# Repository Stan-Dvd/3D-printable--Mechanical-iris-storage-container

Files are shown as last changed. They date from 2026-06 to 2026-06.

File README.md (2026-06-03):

# Mechanical Iris Storage Container
Storage container with dual-plane iris closing mechanism
## Showcase
### Renders:
<p align="center">
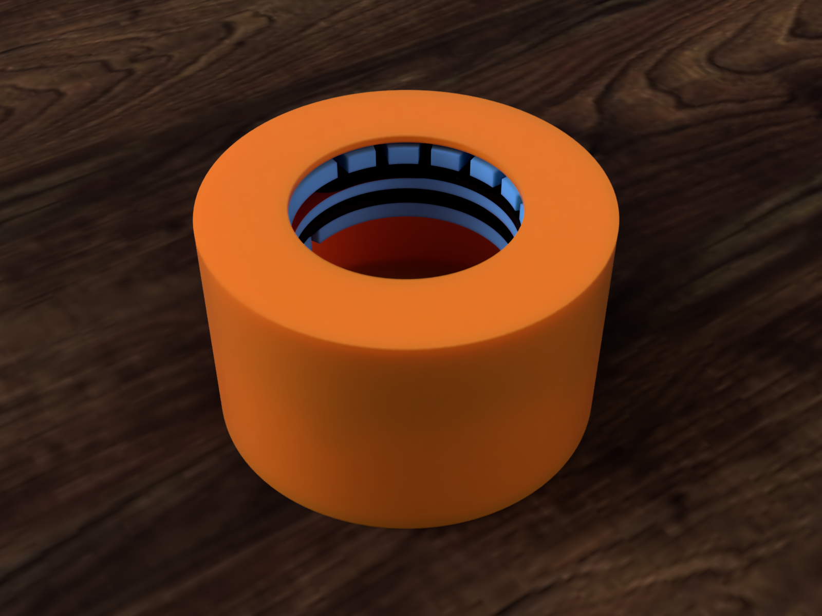
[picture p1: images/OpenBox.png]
  
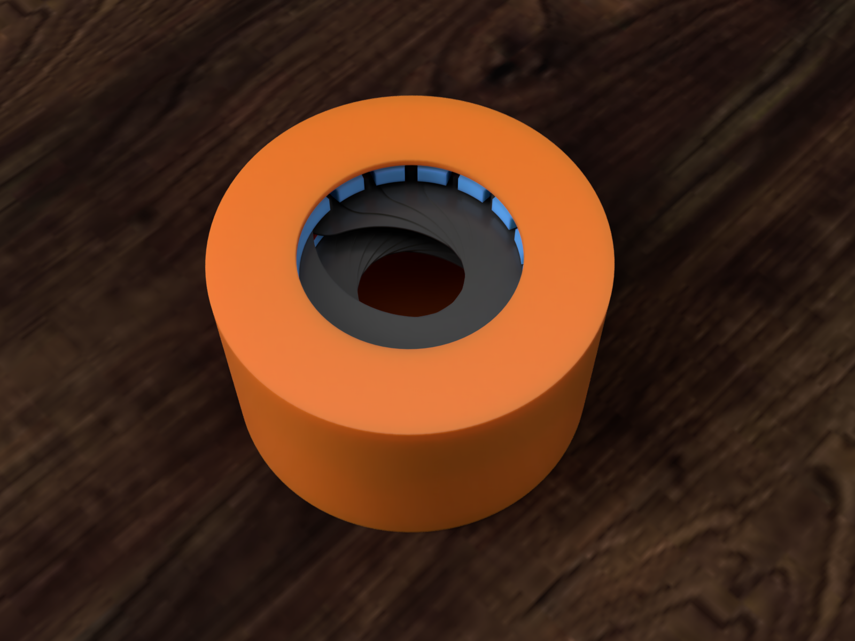
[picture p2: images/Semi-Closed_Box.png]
  
</p>

### Demo video:
Container Demo (https://youtu.be/vQDJuscBDms)

# In short
The basic idea of the project was to create a circular container with a rotating lid that opens and closes an iris mechanism of some form, upon rotating the lid. The idea started upon seeing [this](https://www.printables.com/model/514762-mechanical-iris-container) model on printables (pictured below), and the research started from there

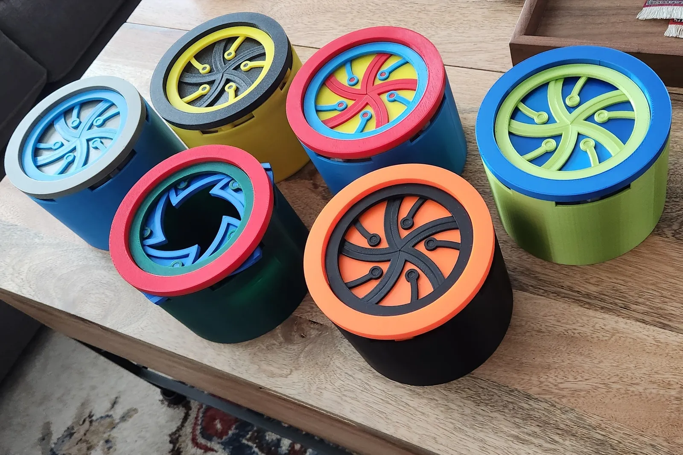
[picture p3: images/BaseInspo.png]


# Design process
The first step of the design process was deciding on the actual iris mechanism to use. The most important part about the mechanism was that I wanted it to be able to fully close. Starting from that, the one from the printables model above was interesting, but I disliked the fact that the blades fanned outward and I couldn't tell how I would build the trajectories for the blades to follow.  Throughout my research, I encountered many mechanisms similar to this one, which I came to name "Rotational translate" irises.
## "Sliding Iris"
The second type of mechanism I encountered was the "sliding iris", where the blades slide along a straight path to partially or completely cover the inner area of the iris. The design was practical and arguably the easiest to implement, but I disliked how once again, it either needed to have a very large ammount of space dedicated to storing the blades, or the blades would have to extend outside of the mechanism.

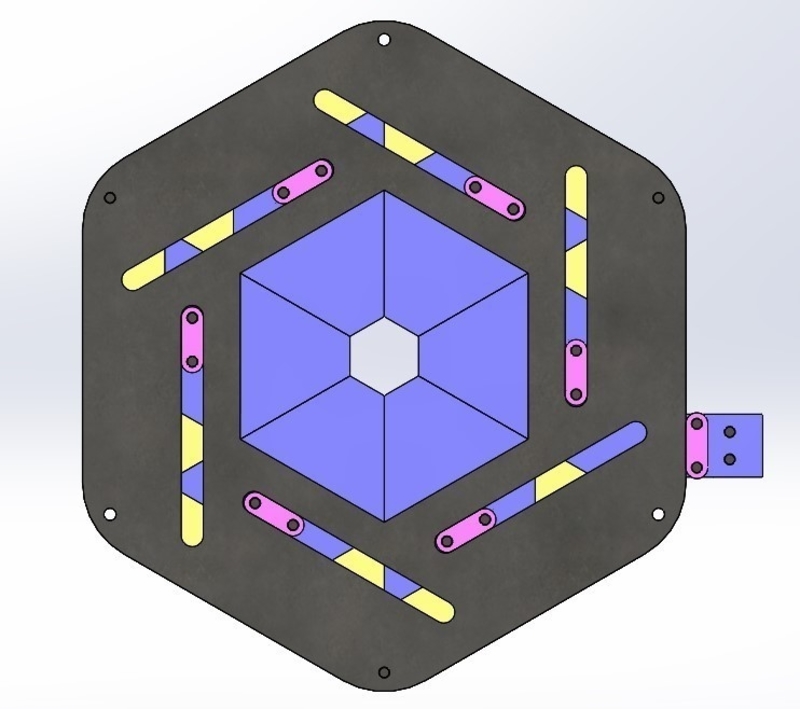
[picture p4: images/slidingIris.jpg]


## Apperture
The third option I found was the traditional camera apperture mechanism. It had the advantage of a small external area but these mechanisms are not designed to close completely. It could be smaller than the others and in theory the most advantageous but ultimately it failed to meet the first requirement - closing completely. This is when I found the mechanism I would eventually choose.

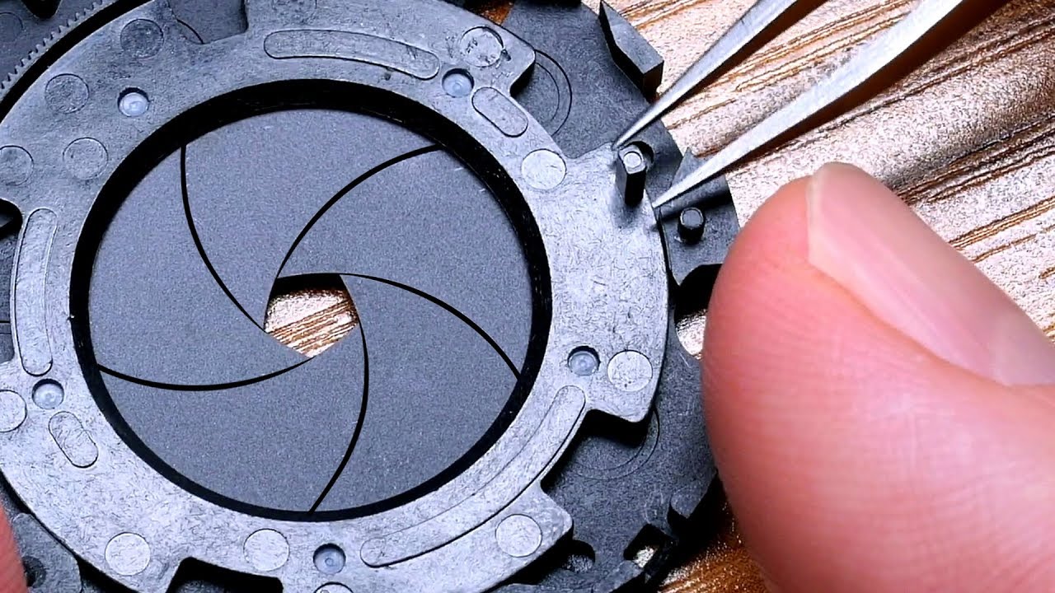
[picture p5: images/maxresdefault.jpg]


## Dual-Plane Iris
The mechanism I eventually chose was the Dual-Plane Iris. It functions very similarly to a regular apperture-type Iris and could generally be designed using the same principles, except it separated the blades into two planes. Half of the blades would sit on one plane, and the other half would sit on the other, while the actuator ring sat in the middle, driving them all. This prevented the blades from overlapping to the point where they wouldn't be able to close, and allowed for a fully closing mechanism

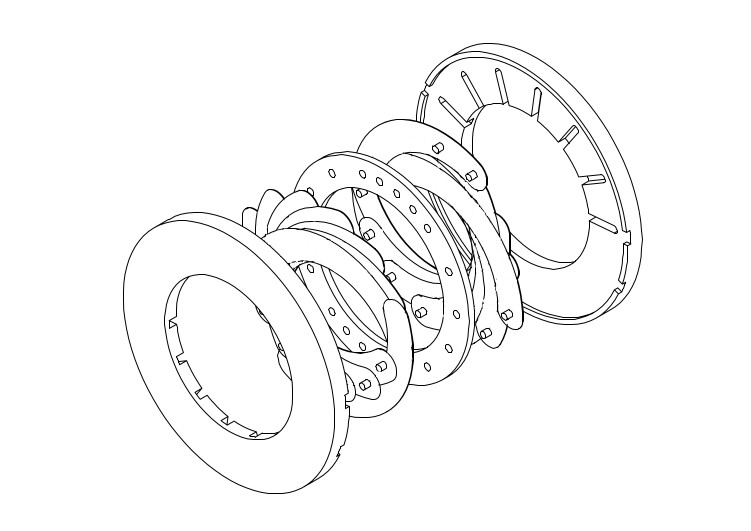
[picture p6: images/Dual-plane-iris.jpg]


# Parts
## Slide rings
The "slide rings" have two roles: allow the blades to move back and forth to follow the actuator ring, and define the axis around which they will be rotating. The dual-plane design requires two slide rings. On a normal apperture mechanism, all of the slots would be on one single ring, but this design places half of the slots on one ring, and half of the slots on the other. The slots on the sides are practically just for the top ring. The body will have two pins that will hold the top ring in place. On that note, it is essential that both slide rings are held in place, the actuator is the only ring that should rotate. However, the slots are found on all the other rings to allow them to be inserted into the body. Additionally, the bottom ring has pin holes on the bottom that will hold it in place relative to the body (not shown)

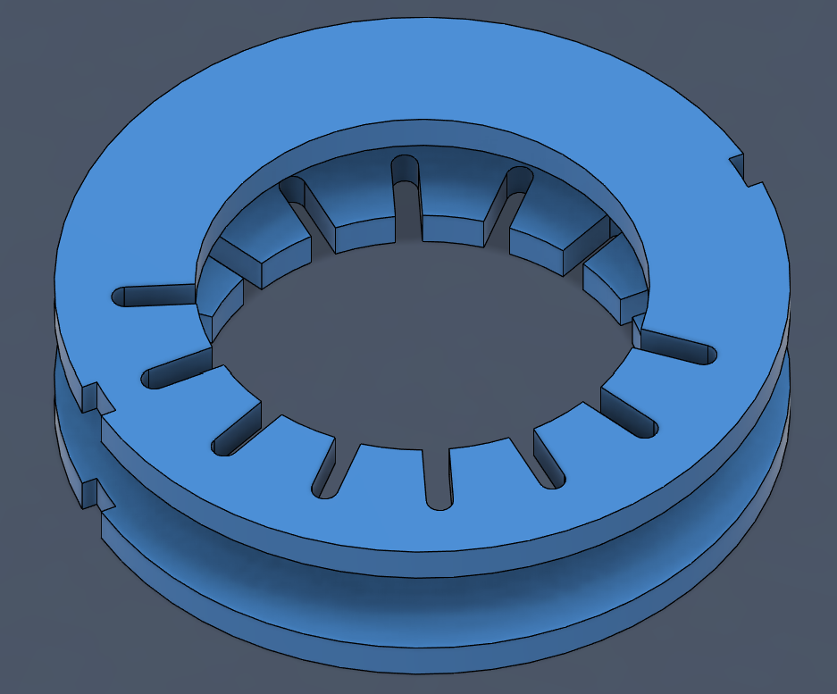
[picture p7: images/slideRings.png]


## Actuator ring
The actuator is the ring that moves the blades, "pulling" them along its' radius and making the iris close. On it, there are 16 pins for each of the regular blades, plus 4 pins that will hold two special "slip-blades", which will be explained later. The inner slots from the slide rings are prezent, as well as two additional outward slots. They will be used to spin the actuator ring from the lid of the container.
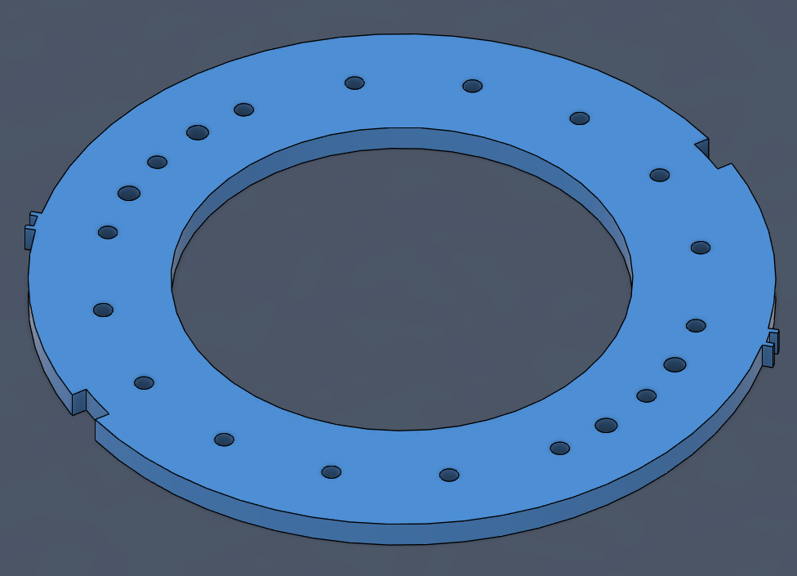
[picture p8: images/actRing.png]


## Blades
### Normal Blades

All of the blades have the same shape, but they differ in how their pins are placed. The bottom blades have their "slide pin" pointing downards and their "actuator pin" pointing upwards. The top blades have their orientations and positions reversed. Additionally, if we were to design the blades in one single piece, they would be very difficult to print because of the two pins on opposing sides. Printing with supports would greatly complicate things, as these pins should be as thin and clean as possible. As such, the actuator pin is to be printed separately, and glued on. To facilitate this, the blade itself has a hole and slot for the pin to fit into, which can be seen on one of the blades pictured below. Another thing to note is that the pins need to be quite long. The blades will be placed on top of each other, and so the pins need to be long enough to reach their respective rings from a decent distance, determined by the thickness and number of blades.

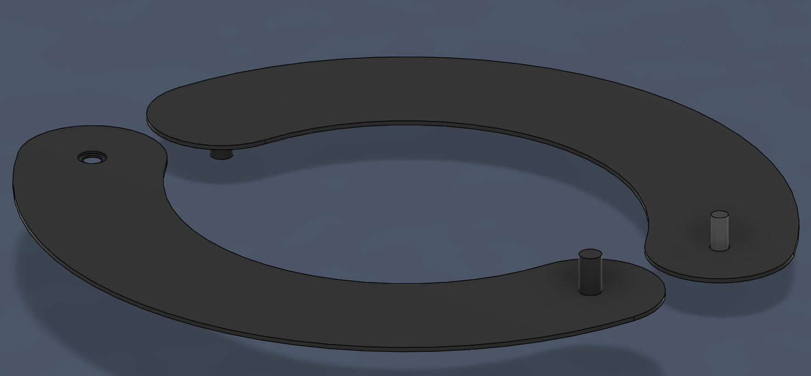
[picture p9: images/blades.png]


### Slip Blades
The slip blades have wo rigid pins on the same side of the blade, again mirroring the pins' position for the top and bottom. Their purpose is to sit on and along the actuator ring, to slip the blades above each other, so the actuator pins don't hit the slide pins. This will make more sense after the mechanism is presented

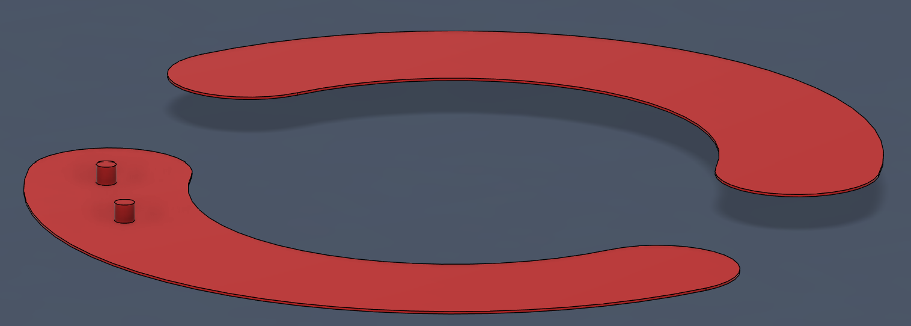
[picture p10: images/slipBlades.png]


## Container body
The container components are in many ways much simpler than the other parts. The container body is a simple cylinder with one side open and a few pins added for holding the top and bottom sliding rings. The bottom ring supports are chamfered at a 45 degree angle, to support 3D printing.

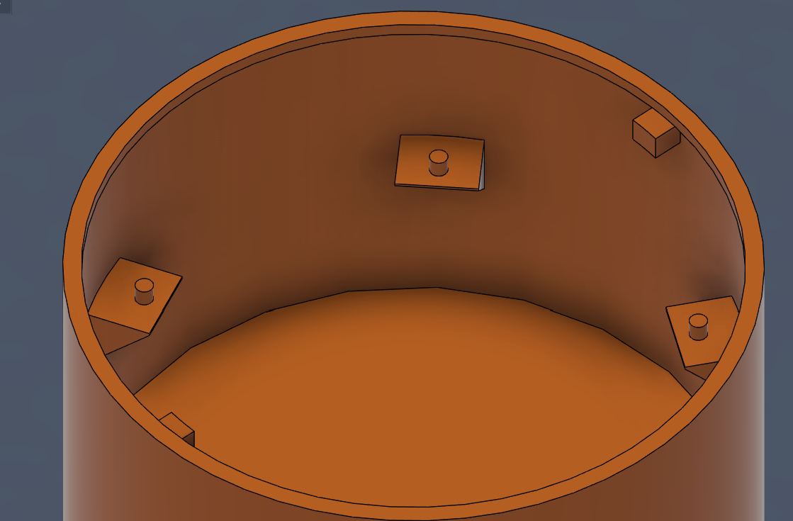
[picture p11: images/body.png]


## Container Cap
The container cap has its' outer diameter equal to the outer diameter of the container and its' inner diameter equal to the inner diameter of the iris mechanism. Additionally, it has an extrusion that is meant to make it slot into the container, without sliding off of it. On top of that, it has two extending pins that reach the actuator ring, so that when the container cap is spun, it spins the actuator ring along with it, practically opening and closing the container

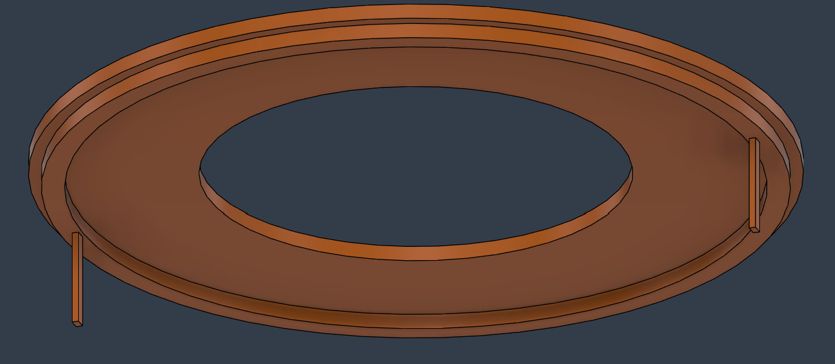
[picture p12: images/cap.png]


# Mechanism assembly and functioning
The blades are placed on top of each other, as shown, so that the slot pins don't hit any of the other blades. In reality, the blades would obviously not stay perfectly straight as shown, but would instead be dragged down by gravity and stay bent. That is intended. This is also the point in which the slip blades start to make sense. As the mechanism is right now, at about 65 degrees of rotation, the blade on the top would hit the slot pin of the blade on the bottom. 

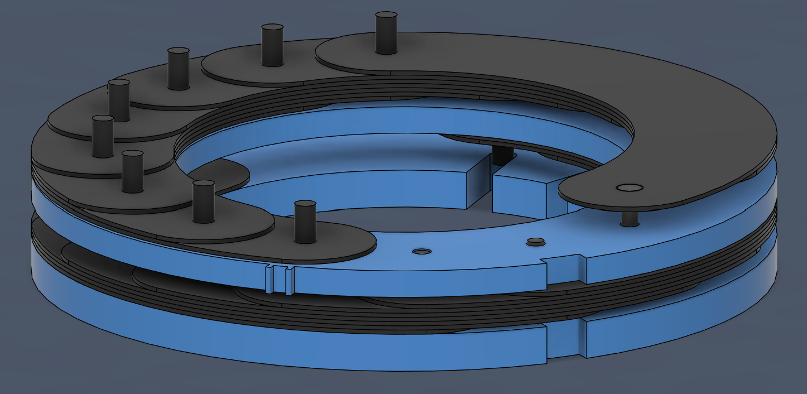
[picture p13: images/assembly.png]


To prevent this, the  slip blade is mounted directly on the actuator ring, below the first blade, and its' other end is placed above the top blade. As such, the top blade(s) will slide downard, below the bottom blade(s). Additionally, because the slip blade rotates with the actuator ring, the top blades do not run into the mounting pins of the slip blade. The slip blade is not shown, because it would have to be bent above the top blade, and I don't know if fusion can do that.
The functioning of the slip blade is similar for the bottom half.

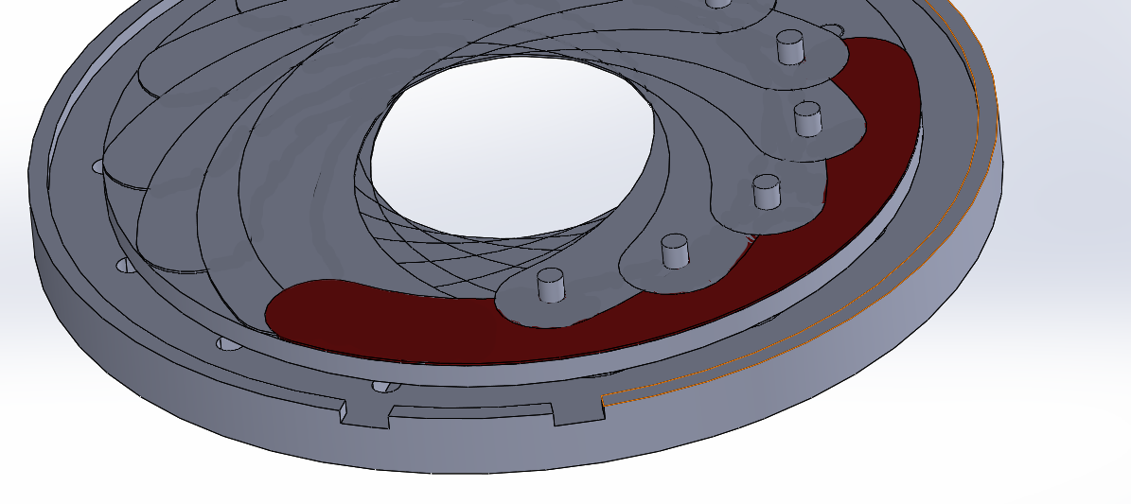
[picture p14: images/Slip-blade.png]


# Notes on the implementation and chosen dimensions
## Blade width 
As I have mentioned in the begining, I didn't want there to be too much space between the inner and outer diameter of the iris, and here, that depends on the width of the blades. Once again, the width of the blades depends on a few things. All of it starts with the closing diameter. The more you want the mechanism to close, logically, the more area the blades will need to cover. As such, the smaller the closing diameter, the thicker the blades need to be. However, this can be offset by the number of blades. A different way of covering the required area is to have more blades, allowing each individual blade to be thinner.
Originally, I started with a 12-blade design. However, once I had everything assembled and could test the entire mechanism, I noticed it didn't fully close. I experimented with making the blades wider, but ultimately felt I had to make them too thick. As such, I decided to switch over to a 16-blade design, and move to a new file. The blades are still wider than I'd like them to be, but I did not have time to experiment more before the deadline
## Blade height
In theory, the blades need to be as thin as possible. The height of the blades entirely determines the height of the entire mechanism, as the distance between each of the rings depends on the height of the blades and how many of them there are. On top of that, the blades cannot be too rigid, as they need to bend. Obviously, the more blades there are, the more critical it is for them to be as thin as possible

My problem in choosing the height of the blades was not knowing exactly how thin it would be reasonable to 3D print something, and how small details can be. Originally, I made the blades .4mm each, but I then realized I needed the slot and pin system to make the design printable. I was not sure if it would be reasonable to make the inner hole of the blade .2mm thick, so I made the blades .8mm and made the inner hole .4mm.
My problem with this is that because of the high thickness and the high number of blades, the iris mechanism itself is much, much taller than I would like it to be. However, I prefered to be safe, and left it like this for now
# Resources
https://www.printables.com/model/143497-mechanical-aperture/files
- base inspiration that sparked the idea for the entire project

https://www.youtube.com/watch?v=vCtbFtSfmnU&t=129s
- fusion tutorial for a 6-blade mechanical iris mechanism
- practically served as the foundation of the entire project

https://iris-calculator.com/full-closure/
 - main (and only) resource for dual-plane iris
 - includes [this](https://web.archive.org/web/20070207011241/http://www.wilkes-iris.com/flashIris/iris.htm) link to an interacteable demonstration of a dual-plane iris

https://www.youtube.com/watch?v=oH6GfyxpK9o 
- microscope aperture assembly, useful as a model for general assembly for these kinds of mechanisms

https://www.printables.com/model/143497-mechanical-aperture/files
- minor inspiration for 3D printed iris mechanism

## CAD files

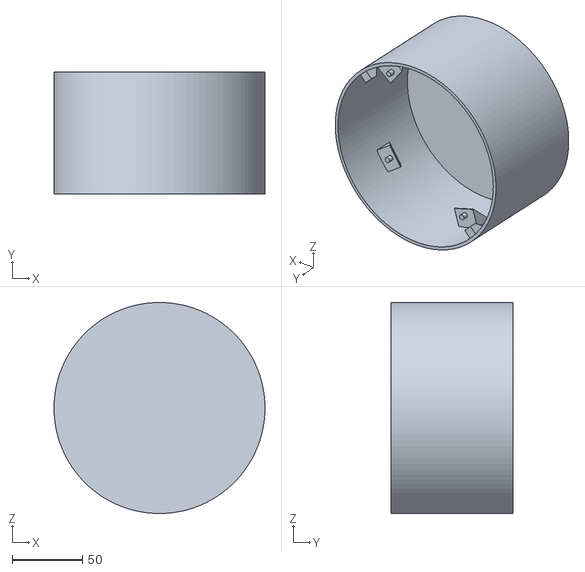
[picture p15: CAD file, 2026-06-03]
STL/Body.stl
150.0 x 87.0 x 150.0

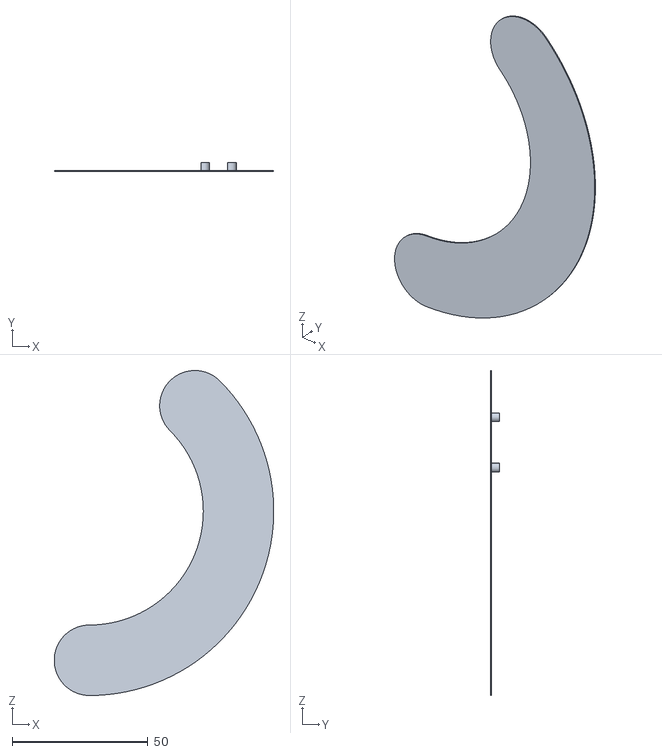
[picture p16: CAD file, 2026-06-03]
STL/SlipBladeBottom.stl
81.0 x 3.40 x 119.9

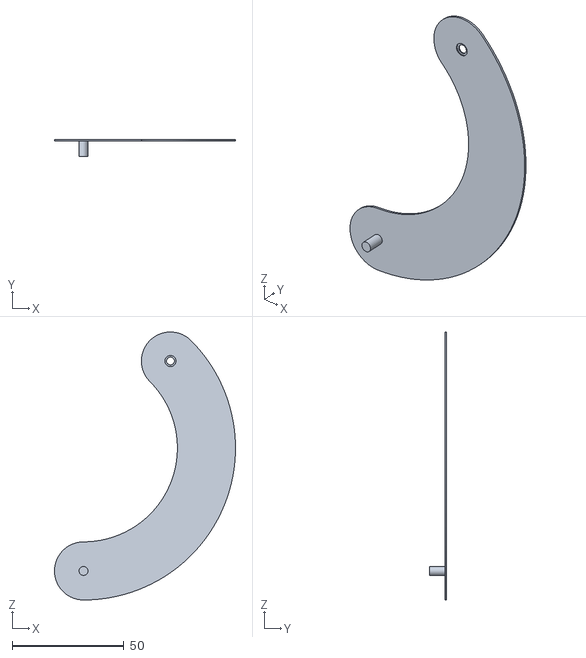
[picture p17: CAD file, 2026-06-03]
STL/BottomBlade.stl
81.0 x 7.80 x 119.9

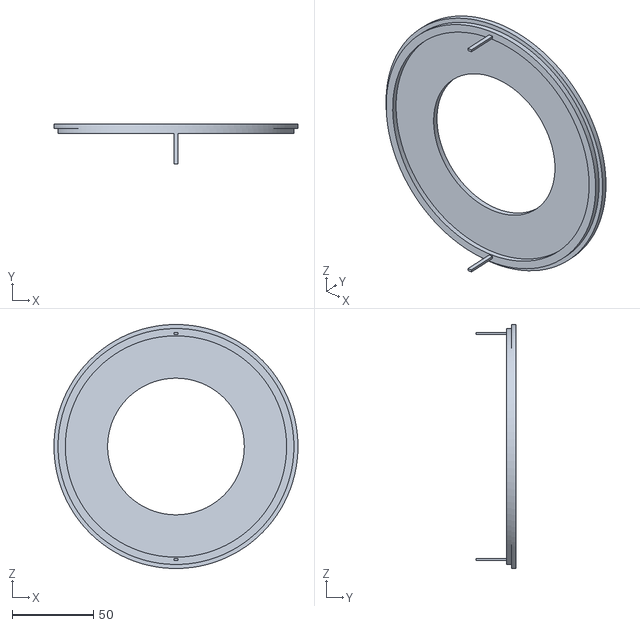
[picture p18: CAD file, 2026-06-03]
STL/TopCap.stl
150.0 x 24.8 x 150.0

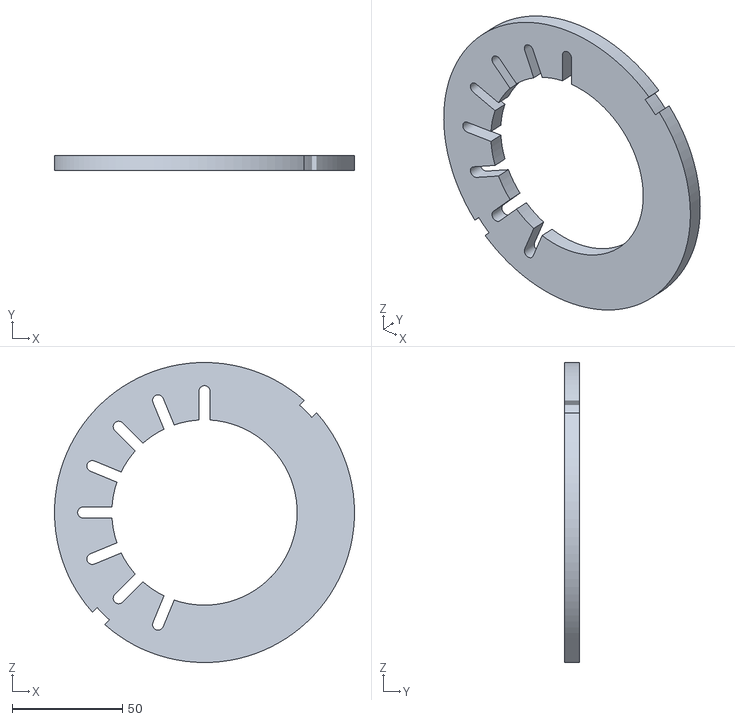
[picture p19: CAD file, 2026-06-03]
STL/TopSlotRing.stl
136.0 x 7.00 x 136.0

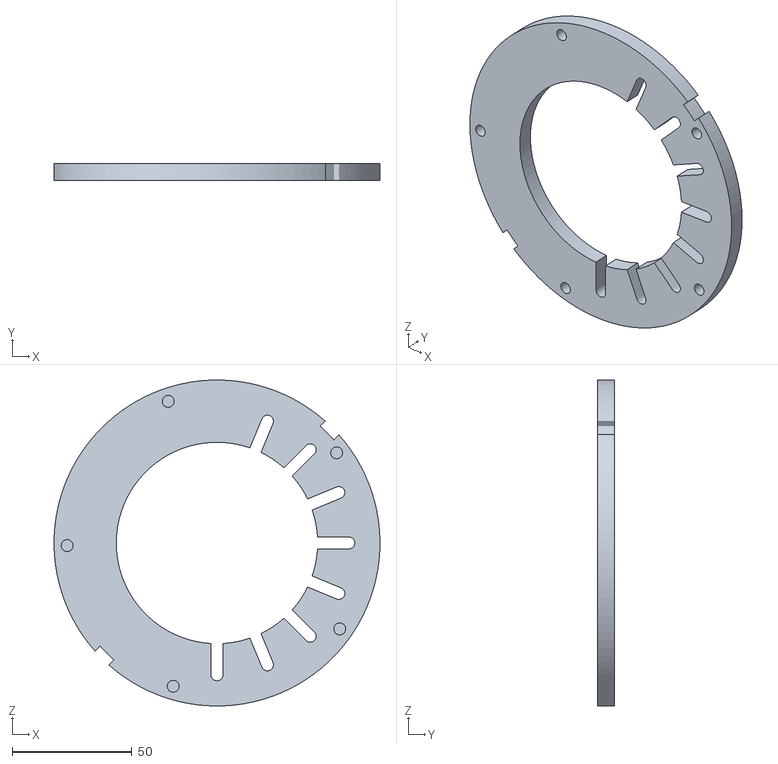
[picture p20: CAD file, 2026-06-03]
STL/BottomSlotRing.stl
136.0 x 7.00 x 136.0

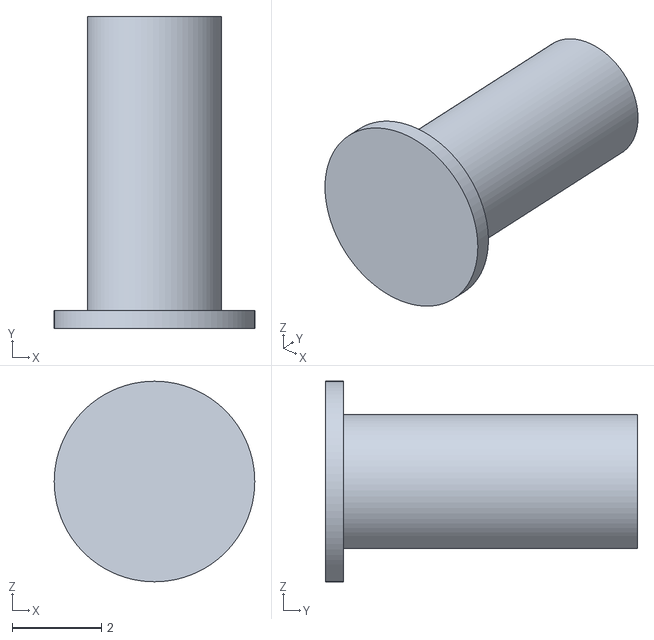
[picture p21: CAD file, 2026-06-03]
STL/Pin.stl
4.50 x 7.00 x 4.50

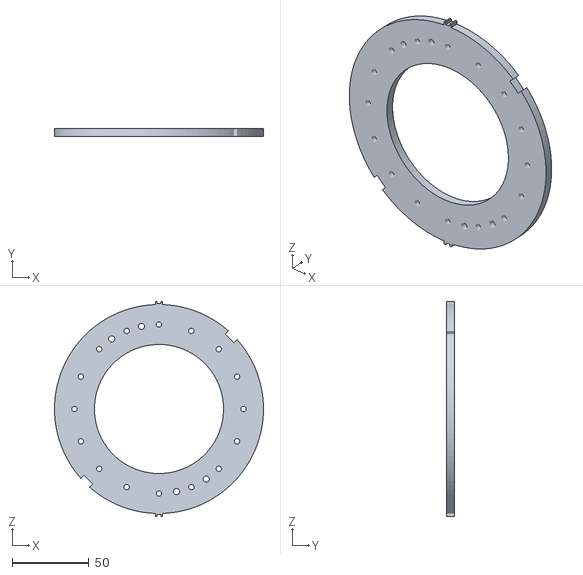
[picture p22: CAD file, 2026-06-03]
STL/ActuatorRing.stl
136.0 x 5.00 x 140.0

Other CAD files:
STL/TopBlade.stl
STL/SlipBladeTop.stl
Container-16BladeIris.f3d

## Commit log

2026-06-03 finished f3d file
    [Container-16BladeIris.f3d]
2026-06-03 Added motion link
    [Container-16BladeIris.f3d]
2026-06-03 Added renders
    [Container-16BladeIris.f3d]
2026-06-03 Added STL files
    [ActuatorRing.stl, Body.stl, BottomBlade.stl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]
2026-06-03 Added G-Code, added chamfer to body
    [Body.stl, Container-16BladeIris.f3d]
